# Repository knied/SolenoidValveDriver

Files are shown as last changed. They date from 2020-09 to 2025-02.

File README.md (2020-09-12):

# SolenoidValveDriver
A PCB to drive Festo MH1 solenoid valves with a "USBIO24 R" (https://www.robotshop.com/de/en/elexol-usb-digital-interface-usbio24-r.html)

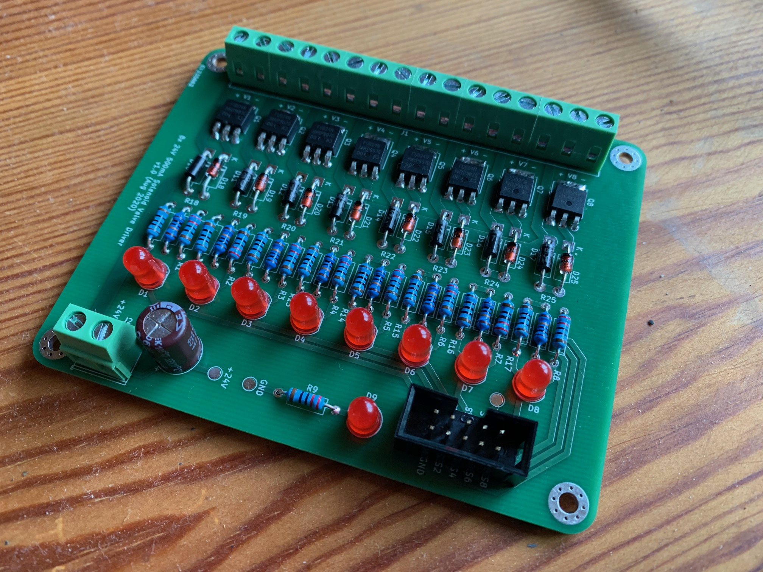
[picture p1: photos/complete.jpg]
Complete Assembly


Symbol | Part | Link
------ | ---- | ----
Q1-Q8 | IRFU024N | https://www.infineon.com/cms/en/product/power/mosfet/12v-300v-n-channel-power-mosfet/irfu024n/
R1-R9 | 220 Ohm |
R10-R17 | 100 Ohm | 
R18-R25 | 100k Ohm |
D1-D9 | 5mm Red LED |
D10-D17 | 1N4937 | https://www.vishay.com/docs/88508/1n4933.pdf
D18-D25 | 1N4748 | https://www.futurlec.com/Diodes/1N4748.shtml
C1 | 100uF |
J1 | 16x TerminalBlock (5.08mm) |
J2 | 2x TerminalBlock (5.08mm) |
J3 | 2x5 Pin Header (2.54mm) |

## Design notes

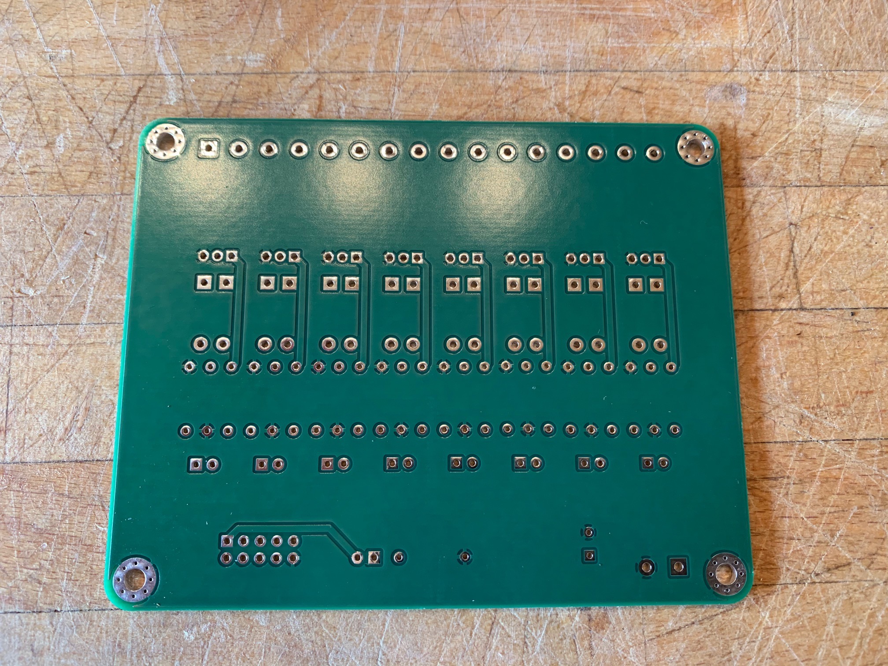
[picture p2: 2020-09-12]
photos/back.jpg

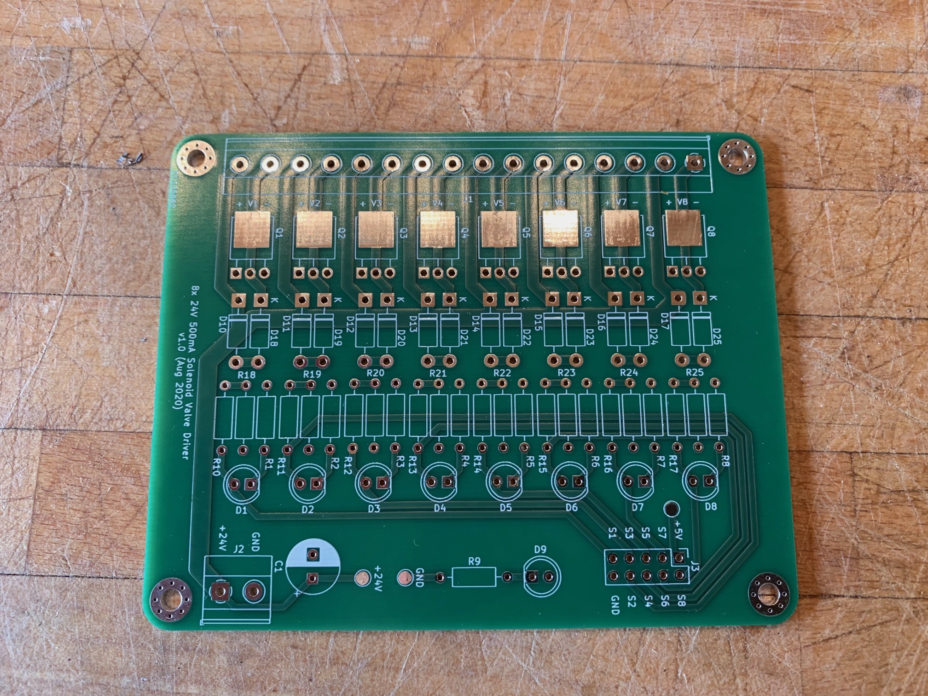
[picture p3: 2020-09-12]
photos/front.jpg

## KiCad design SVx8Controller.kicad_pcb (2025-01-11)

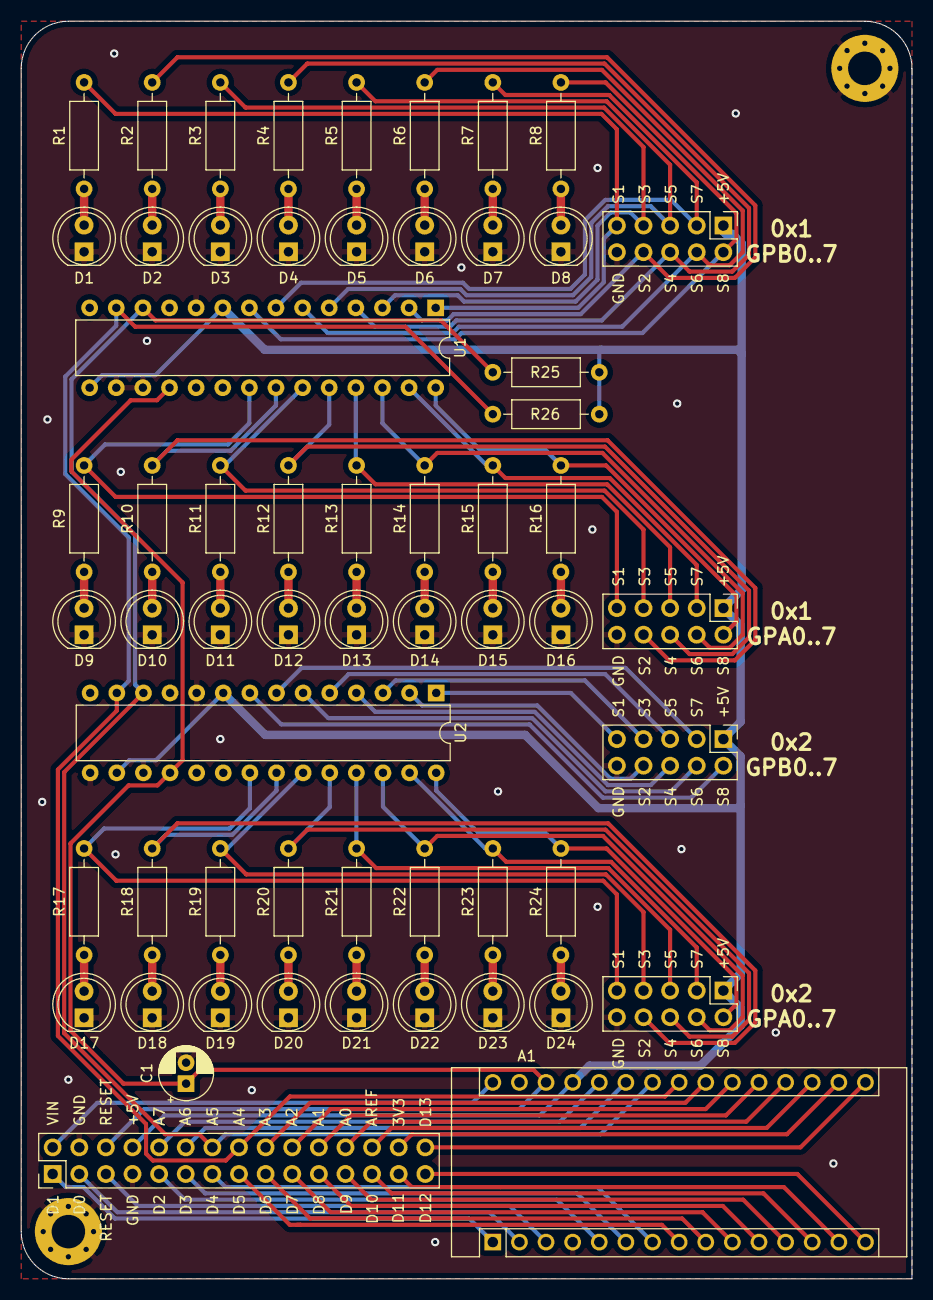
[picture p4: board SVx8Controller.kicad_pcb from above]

Board: 2 copper layers, 85.0 x 120.0 mm, 61 parts (0 on the bottom side), 85 nets.

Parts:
A1: Arduino_Nano_v3.x; Arduino_Nano
C1: 10uF; CP_Radial_D5.0mm_P2.00mm
D1, D2, D3, D4, D5, D6, D7, D8, D9, D10, D11, D12, D13, D14, D15, D16, D17, D18, D19, D20, D21, D22, D23, D24: LED; LED_D5.0mm
H1, H2: MountingHole_Pad; MountingHole_3.2mm_M3_Pad_Via
J1, J2, J3: Output; PinHeader_2x05_P2.54mm_Vertical
J4: Conn_01x10; PinHeader_2x05_P2.54mm_Vertical
J5: Conn_01x30; PinHeader_2x15_P2.54mm_Vertical
R1, R2, R3, R4, R5, R6, R7, R8, R9, R10, R11, R12, R13, R14, R15, R16, R17, R18, R19, R20, R21, R22, R23, R24: 220; R_Axial_DIN0207_L6.3mm_D2.5mm_P10.16mm_Horizontal
R25, R26: 10K; R_Axial_DIN0207_L6.3mm_D2.5mm_P10.16mm_Horizontal
U1, U2: MCP23017_SP; DIP-28_W7.62mm

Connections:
3V3: A1.17, J5.28
5V: A1.27, J1.1, J2.1, J3.1, J4.1, J5.8, R25.2, R26.2, U1.9, U1.15, U2.9, U2.16
/Port A/SIG1: J1.9, R9.2, U1.21
/Port A/SIG2: J1.8, R10.2, U1.22
/Port A/SIG3: J1.7, R11.2, U1.23
/Port A/SIG4: J1.6, R12.2, U1.24
/Port A/SIG5: J1.5, R13.2, U1.25
/Port A/SIG6: J1.4, R14.2, U1.26
/Port A/SIG7: J1.3, R15.2, U1.27
/Port A/SIG8: J1.2, R16.2, U1.28
/Port B/SIG1: J2.9, R1.2, U1.1
/Port B/SIG2: J2.8, R2.2, U1.2
/Port B/SIG3: J2.7, R3.2, U1.3
/Port B/SIG4: J2.6, R4.2, U1.4
/Port B/SIG5: J2.5, R5.2, U1.5
/Port B/SIG6: J2.4, R6.2, U1.6
/Port B/SIG7: J2.3, R7.2, U1.7
/Port B/SIG8: J2.2, R8.2, U1.8
/Port C/SIG1: J3.9, R17.2, U2.21
/Port C/SIG2: J3.8, R18.2, U2.22
/Port C/SIG3: J3.7, R19.2, U2.23
/Port C/SIG4: J3.6, R20.2, U2.24
/Port C/SIG5: J3.5, R21.2, U2.25
/Port C/SIG6: J3.4, R22.2, U2.26
/Port C/SIG7: J3.3, R23.2, U2.27
/Port C/SIG8: J3.2, R24.2, U2.28
A0: A1.19, J5.24
A1: A1.20, J5.22
A2: A1.21, J5.20
A3: A1.22, J5.18
A4: A1.23, J5.16, R26.1, U1.13, U2.13
A5: A1.24, J5.14, R25.1, U1.12, U2.12
A6: A1.25, J5.12
A7: A1.26, J5.10
AREF: A1.18, J5.26
D0: A1.2, J5.3
D1: A1.1, J5.1
D2: A1.5, J5.9
D3: A1.6, J5.11
D4: A1.7, J5.13
D5: A1.8, J5.15
D6: A1.9, J5.17
D7: A1.10, J5.19
D8: A1.11, J5.21
D9: A1.12, J5.23
D10: A1.13, J5.25
D11: A1.14, J5.27
D12: A1.15, J5.29
D13: A1.16, J5.30
GND: A1.4, A1.29, C1.2, D1.1, D2.1, D3.1, D4.1, D5.1, D6.1, D7.1, D8.1, D9.1, D10.1, D11.1, D12.1, D13.1, D14.1, D15.1, D16.1, D17.1, D18.1, D19.1, D20.1, D21.1, D22.1, D23.1, D24.1, H1.1, H2.1, J1.10, J2.10, J3.10, J4.10, J5.4, J5.7, U1.10, U1.16, U1.17, U2.10, U2.15, U2.17
unnamed: D1.2, R1.1
unnamed: D2.2, R2.1
unnamed: D3.2, R3.1
unnamed: D4.2, R4.1
unnamed: D5.2, R5.1
unnamed: D6.2, R6.1
unnamed: D7.2, R7.1
unnamed: D8.2, R8.1
unnamed: D9.2, R9.1
unnamed: D10.2, R10.1
unnamed: D11.2, R11.1
unnamed: D12.2, R12.1
unnamed: D13.2, R13.1
unnamed: D14.2, R14.1
unnamed: D15.2, R15.1
unnamed: D16.2, R16.1
unnamed: D17.2, R17.1
unnamed: D18.2, R18.1
unnamed: D19.2, R19.1
unnamed: D20.2, R20.1
unnamed: D21.2, R21.1
unnamed: D22.2, R22.1
unnamed: D23.2, R23.1
unnamed: D24.2, R24.1
PD1: J4.9, U2.1
PD2: J4.8, U2.2
PD3: J4.7, U2.3
PD4: J4.6, U2.4
PD5: J4.5, U2.5
PD6: J4.4, U2.6
PD7: J4.3, U2.7
PD8: J4.2, U2.8
RESET: A1.28, C1.1, J5.6, U1.18, U2.18
RESET2: A1.3, J5.5
VIN: A1.30, J5.2

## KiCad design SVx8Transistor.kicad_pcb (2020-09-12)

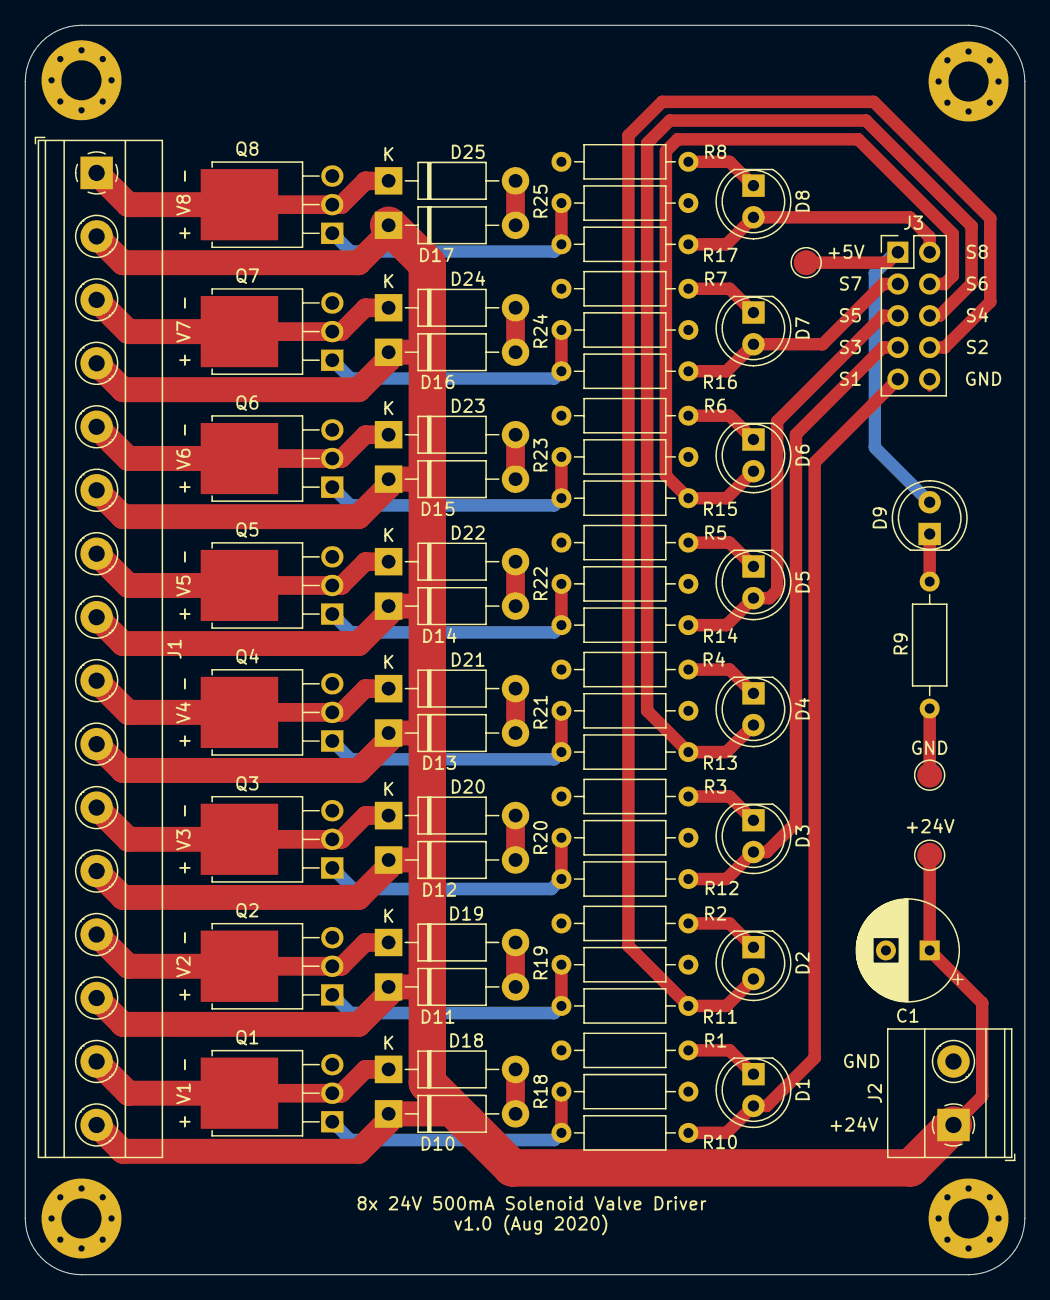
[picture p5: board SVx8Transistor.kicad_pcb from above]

Board: 2 copper layers, 80.0 x 100.0 mm, 69 parts (0 on the bottom side), 44 nets.

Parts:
C1: 100uF; CP_Radial_D8.0mm_P3.50mm
D1, D2, D3, D4, D5, D6, D7, D8, D9: LED; LED_D5.0mm
D10, D11, D12, D13, D14, D15, D16, D17: 1N4937; D_DO-41_SOD81_P10.16mm_Horizontal
D18, D19, D20, D21, D22, D23, D24, D25: 1N4748; D_DO-41_SOD81_P10.16mm_Horizontal
H1, H2, H3, H4: MountingHole_Pad; MountingHole_3.2mm_M3_Pad_Via
J1: Valves; TerminalBlock_Phoenix_MKDS-1,5-16-5.08_1x16_P5.08mm_Horizon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
J2: Power; TerminalBlock_Phoenix_MKDS-1,5-2-5.08_1x02_P5.08mm_Horizont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
J3: Signals; PinHeader_2x05_P2.54mm_Vertical
Q1, Q2, Q3, Q4, Q5, Q6, Q7, Q8: IRFU024N; TO-251-3-1EP_Horizontal_TabDown
R1, R2, R3, R4, R5, R6, R7, R8, R9: 220; R_Axial_DIN0207_L6.3mm_D2.5mm_P10.16mm_Horizontal
R10, R11, R12, R13, R14, R15, R16, R17: 100; R_Axial_DIN0207_L6.3mm_D2.5mm_P10.16mm_Horizontal
R18, R19, R20, R21, R22, R23, R24, R25: 100k; R_Axial_DIN0207_L6.3mm_D2.5mm_P10.16mm_Horizontal
TP1: GND; TestPoint_Pad_D2.0mm
TP2: +24V; TestPoint_Pad_D2.0mm
TP3: +5V; TestPoint_Pad_D2.0mm

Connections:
5V: D9.2, J3.1, TP3.1
GND: C1.2, H1.1, H2.1, H3.1, H4.1, J2.2, J3.10, Q1.3, Q2.3, Q3.3, Q4.3, Q5.3, Q6.3, Q7.3, Q8.3, R1.2, R2.2, R3.2, R4.2, R5.2, R6.2, R7.2, R8.2, R9.2, R18.2, R19.2, R20.2, R21.2, R22.2, R23.2, R24.2, R25.2, TP1.1
unnamed: D1.1, R1.1
unnamed: D2.1, R2.1
unnamed: D3.1, R3.1
unnamed: D4.1, R4.1
unnamed: D5.1, R5.1
unnamed: D6.1, R6.1
unnamed: D7.1, R7.1
unnamed: D8.1, R8.1
unnamed: D9.1, R9.1
unnamed: D10.2, D18.2
unnamed: D11.2, D19.2
unnamed: D12.2, D20.2
unnamed: D13.2, D21.2
unnamed: D14.2, D22.2
unnamed: D15.2, D23.2
unnamed: D16.2, D24.2
unnamed: D17.2, D25.2
unnamed: Q1.1, R10.1, R18.1
unnamed: Q2.1, R11.1, R19.1
unnamed: Q3.1, R12.1, R20.1
unnamed: Q4.1, R13.1, R21.1
unnamed: Q5.1, R14.1, R22.1
unnamed: Q6.1, R15.1, R23.1
unnamed: Q7.1, R16.1, R24.1
unnamed: Q8.1, R17.1, R25.1
SIG1: D1.2, J3.9, R10.2
SIG2: D2.2, J3.8, R11.2
SIG3: D3.2, J3.7, R12.2
SIG4: D4.2, J3.6, R13.2
SIG5: D5.2, J3.5, R14.2
SIG6: D6.2, J3.4, R15.2
SIG7: D7.2, J3.3, R16.2
SIG8: D8.2, J3.2, R17.2
VCC: C1.1, D10.1, D11.1, D12.1, D13.1, D14.1, D15.1, D16.1, D17.1, J1.2, J1.4, J1.6, J1.8, J1.10, J1.12, J1.14, J1.16, J2.1, TP2.1
Valve1_Black: D18.1, J1.15, Q1.2, Q1.4
Valve2_Black: D19.1, J1.13, Q2.2, Q2.4
Valve3_Black: D20.1, J1.11, Q3.2, Q3.4
Valve4_Black: D21.1, J1.9, Q4.2, Q4.4
Valve5_Black: D22.1, J1.7, Q5.2, Q5.4
Valve6_Black: D23.1, J1.5, Q6.2, Q6.4
Valve7_Black: D24.1, J1.3, Q7.2, Q7.4
Valve8_Black: D25.1, J1.1, Q8.2, Q8.4

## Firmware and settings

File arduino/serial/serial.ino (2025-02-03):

#include <Wire.h>

namespace mcp23017 {

enum reg : uint8_t {
  IODIR_A   = 0x00,
  IODIR_B   = 0x01,
  IOCON     = 0x0A,
  GPIO_A    = 0x12,
  GPIO_B    = 0x13,
};

static void writeRegister(uint8_t addr, uint8_t reg, uint8_t value) {
  Wire.beginTransmission(addr);
  Wire.write(reg);
  Wire.write(value);
  Wire.endTransmission();
}

static void initDevice(uint8_t addr) {
  // Bit | Configure:
  //   7 | BANK   = 0
  //   6 | MIRROR = 0
  //   5 | SEQOP  = 1
  //   4 | DISSLW = 0
  //   3 | HAEN   = 0
  //   2 | ODR    = 0
  //   1 | INTPOL = 0
  //   0 | ---
  writeRegister(addr, reg::IOCON, 0b00100000);
  // Configure all bits as output:
  writeRegister(addr, reg::IODIR_A, 0b00000000);
  writeRegister(addr, reg::IODIR_B, 0b00000000);
}

} // namespace mcp23017

void setup() {
  // start serial port at 9600 bps:
  Serial.begin(9600);
  while (!Serial) {
    ;  // wait for serial port to connect. Needed for native USB port only
  }

#if 0
  // Setup Port A
  for (int pin = 2; pin < 10; ++pin) {
    pinMode(pin, OUTPUT);
    digitalWrite(pin, LOW);
  }
#else
  // Setup I2C 
  Wire.begin();
  mcp23017::initDevice(0x21);
  mcp23017::initDevice(0x22);
#endif
}

void setPort(int port, unsigned char value) {
#if 0
  if (port == 0) {
    // Port A
    for (int pin = 0; pin < 8; ++pin) {
      int level = (value & (1 << pin)) == 0 ? LOW : HIGH;
      digitalWrite(pin + 2, level); // pins 2..9
    }
  } else {
    // Ports B..C not supported yet
  }
#else
  uint8_t addr[] = {
    0x21, // A
    0x21, // B
    0x22, // C
    0x22  // D
  };
  mcp23017::reg reg[] = {
    mcp23017::reg::GPIO_A, // A
    mcp23017::reg::GPIO_B, // B
    mcp23017::reg::GPIO_A, // C
    mcp23017::reg::GPIO_B  // D
  };
  mcp23017::writeRegister(addr[port], reg[port], value);
#endif
}

unsigned char portValue[4] = {};
unsigned char portDir[4] = {};
int receivePort = 0;
enum CommandState {
  READY, RECEIVE_VALUE, DIR, RECEIVE_DIR
};
CommandState state = READY;
void loop() {
  if (Serial.available() > 0) {
    char inByte = Serial.read();
    if (state == READY) {
      switch (inByte) {
        case '?': {
          Serial.print("USB I/O 24");
        } break;
        case 'A': {
          state = RECEIVE_VALUE;
          receivePort = 0; // A
        } break;
        case 'B': {
          state = RECEIVE_VALUE;
          receivePort = 1; // B
        } break;
        case 'C': {
          state = RECEIVE_VALUE;
          receivePort = 2; // C
        } break;
        case 'D': {
          state = RECEIVE_VALUE;
          receivePort = 3; // D
        } break;
        case 'a': {
          Serial.write(portValue[0]);
        } break;
        case 'b': {
          Serial.write(portValue[1]);
        } break;
        case 'c': {
          Serial.write(portValue[2]);
        } break;
        case 'd': {
          Serial.write(portValue[3]);
        } break;
        case '!': {
          state = DIR;
        } break;
        default: break;
      }      
    } else if (state == RECEIVE_VALUE) {
      portValue[receivePort] = inByte;
      setPort(receivePort, inByte);
      state = READY;
    } else if (state == DIR) {
      switch (inByte) {
        case 'A': {
          state = RECEIVE_DIR;
          receivePort = 0;
        } break;
        case 'B': {
          state = RECEIVE_DIR;
          receivePort = 1;
        } break;
        case 'C': {
          state = RECEIVE_DIR;
          receivePort = 2;
        } break;
        case 'D': {
          state = RECEIVE_DIR;
          receivePort = 3;
        } break;
        default: {
          state = READY;
          break;
        }
      }
    } else if (state == RECEIVE_DIR) {
      // We only need outputs. Ignored for now...
      state = READY;
    } else {
      state = READY;
    }
    
#if 0
    if (inByte == '0') {
      Serial.println("OFF");
      state = LOW;
      digitalWrite(PIN_A0, state);
    } else if (inByte == '1') {
      Serial.println("ON");
      state = HIGH;
      digitalWrite(PIN_A0, state);
    }
#endif
  }
}

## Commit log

2025-01-11 Add a controller PCB (#1)
    * Add controller front plate
    * Fix pin header
    * Add pull-up resistors
    [DisplayChannel.sch, SVx8Controller.kicad_pcb, SVx8Controller.sch]
2025-01-11 Fix edge cut widths
    [SVx8Controller.kicad_pcb]
2025-02-03 Add a program for the Arduino Nano
    It mimics the behavior of a USBIO24.
